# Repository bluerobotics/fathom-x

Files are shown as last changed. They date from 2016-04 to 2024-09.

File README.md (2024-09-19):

# Fathom-X and Fathom-E

The Fathom-X and -E Tether Boards are part of Blue Robotics' *Fathom Tether* system. These boards provide interfaces and functionality for the communication methods used with the tether. With the Fathom tether, it is quick and easy to get up and running and interface with your ROV or other application.

The schematic and board layout are designed in EagleCAD.

# Fathom-E (Simple Ethernet) Hardware

## Description

The Fathom-E board provides a simple and economical way to connect the Fathom Tether or a Cat5 cable to an Ethernet jack. It uses all four twisted pairs in the cable and works for tether lengths of up to 100m (per the Ethernet specification).

# Fathom-X Hardware

The Fathom-X board has a few advantages over the Fathom-E interface. It uses a HomePlugAV (IEEE1901) module to send 100 Mbps Ethernet with a single twisted pair. This robust connection works over at least 300m tether lengths. 

Please see the [official documentation](http://docs.bluerobotics.com/fathom-x/) for more information.

## License

The Fathom Ethernet Hardware Design is released under the MIT License.

## Revision History

### Fathom-E 

rev1 - Works but RJ45 misaligned

rev2 - Production version

### Fathom-X

rev1 - Works but poor tether connector used

rev2 - Production version with updated connector

RevB - In progress

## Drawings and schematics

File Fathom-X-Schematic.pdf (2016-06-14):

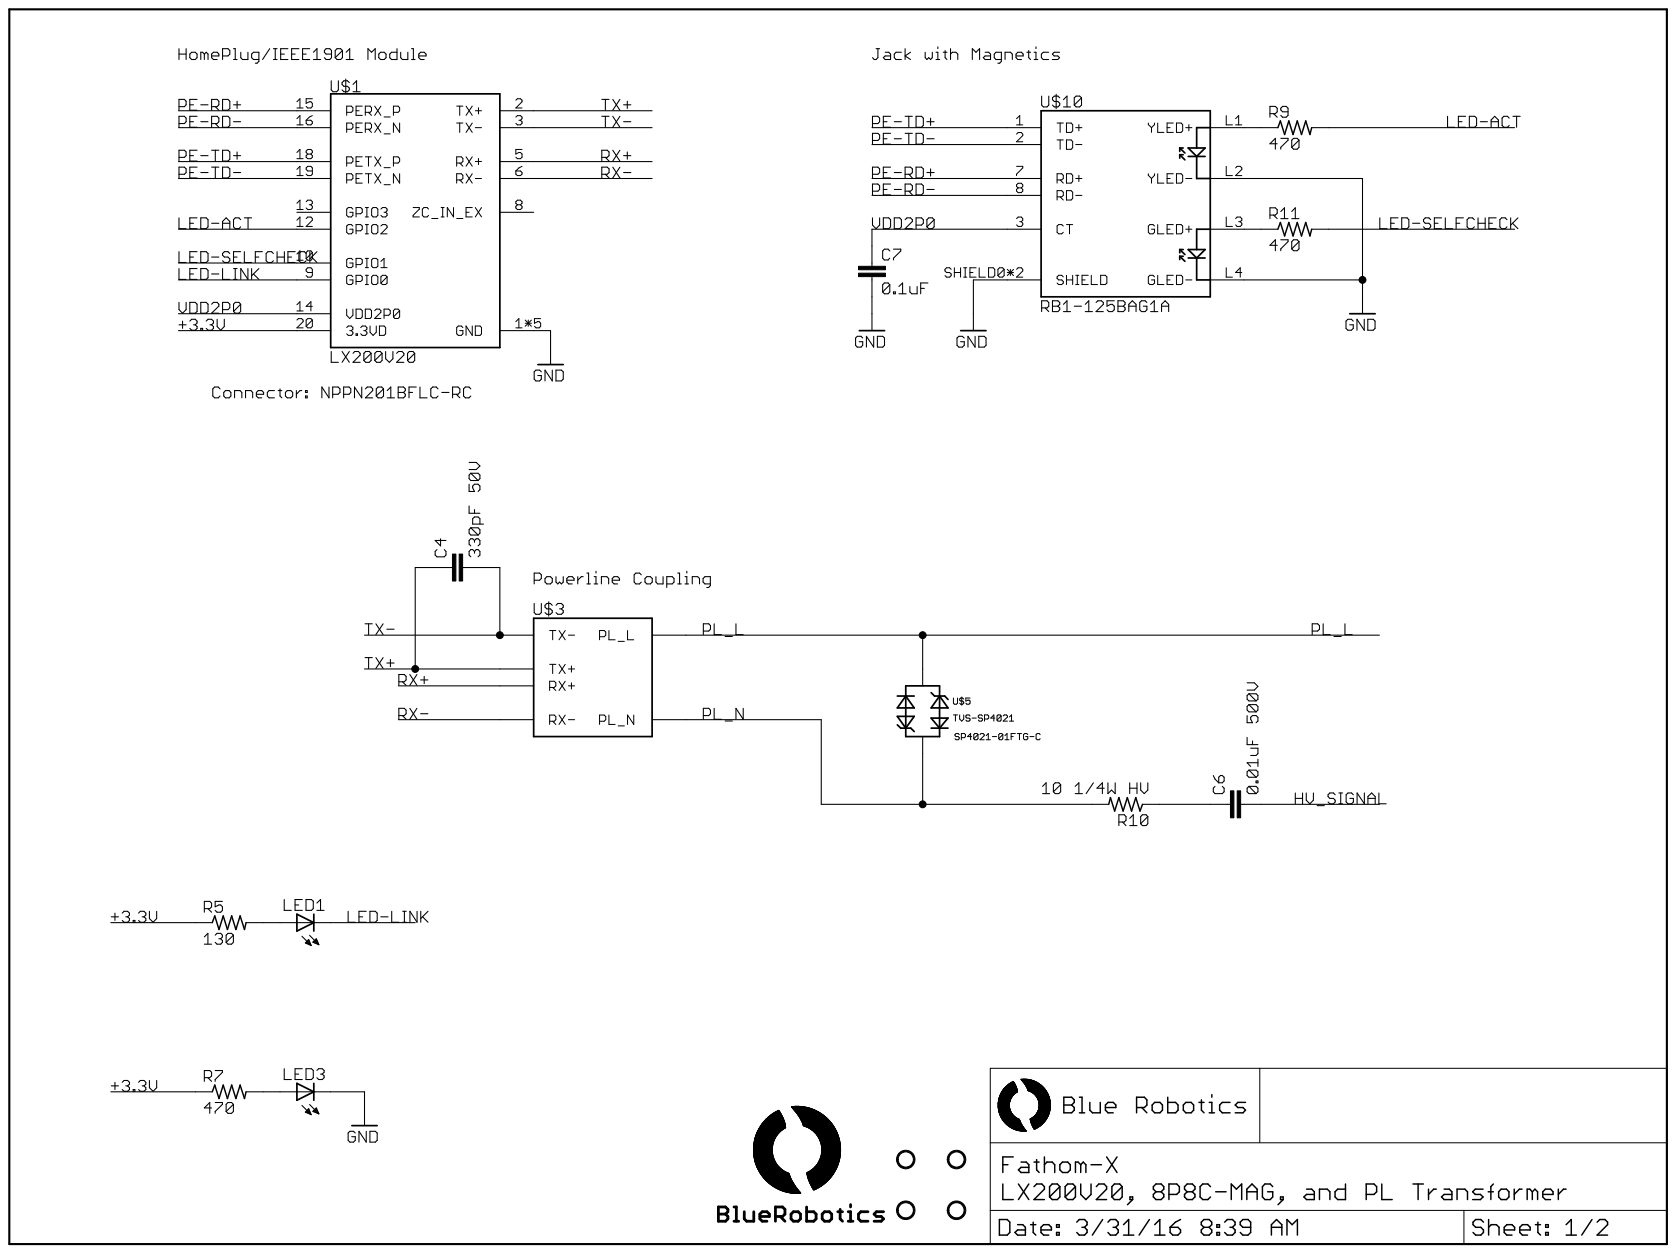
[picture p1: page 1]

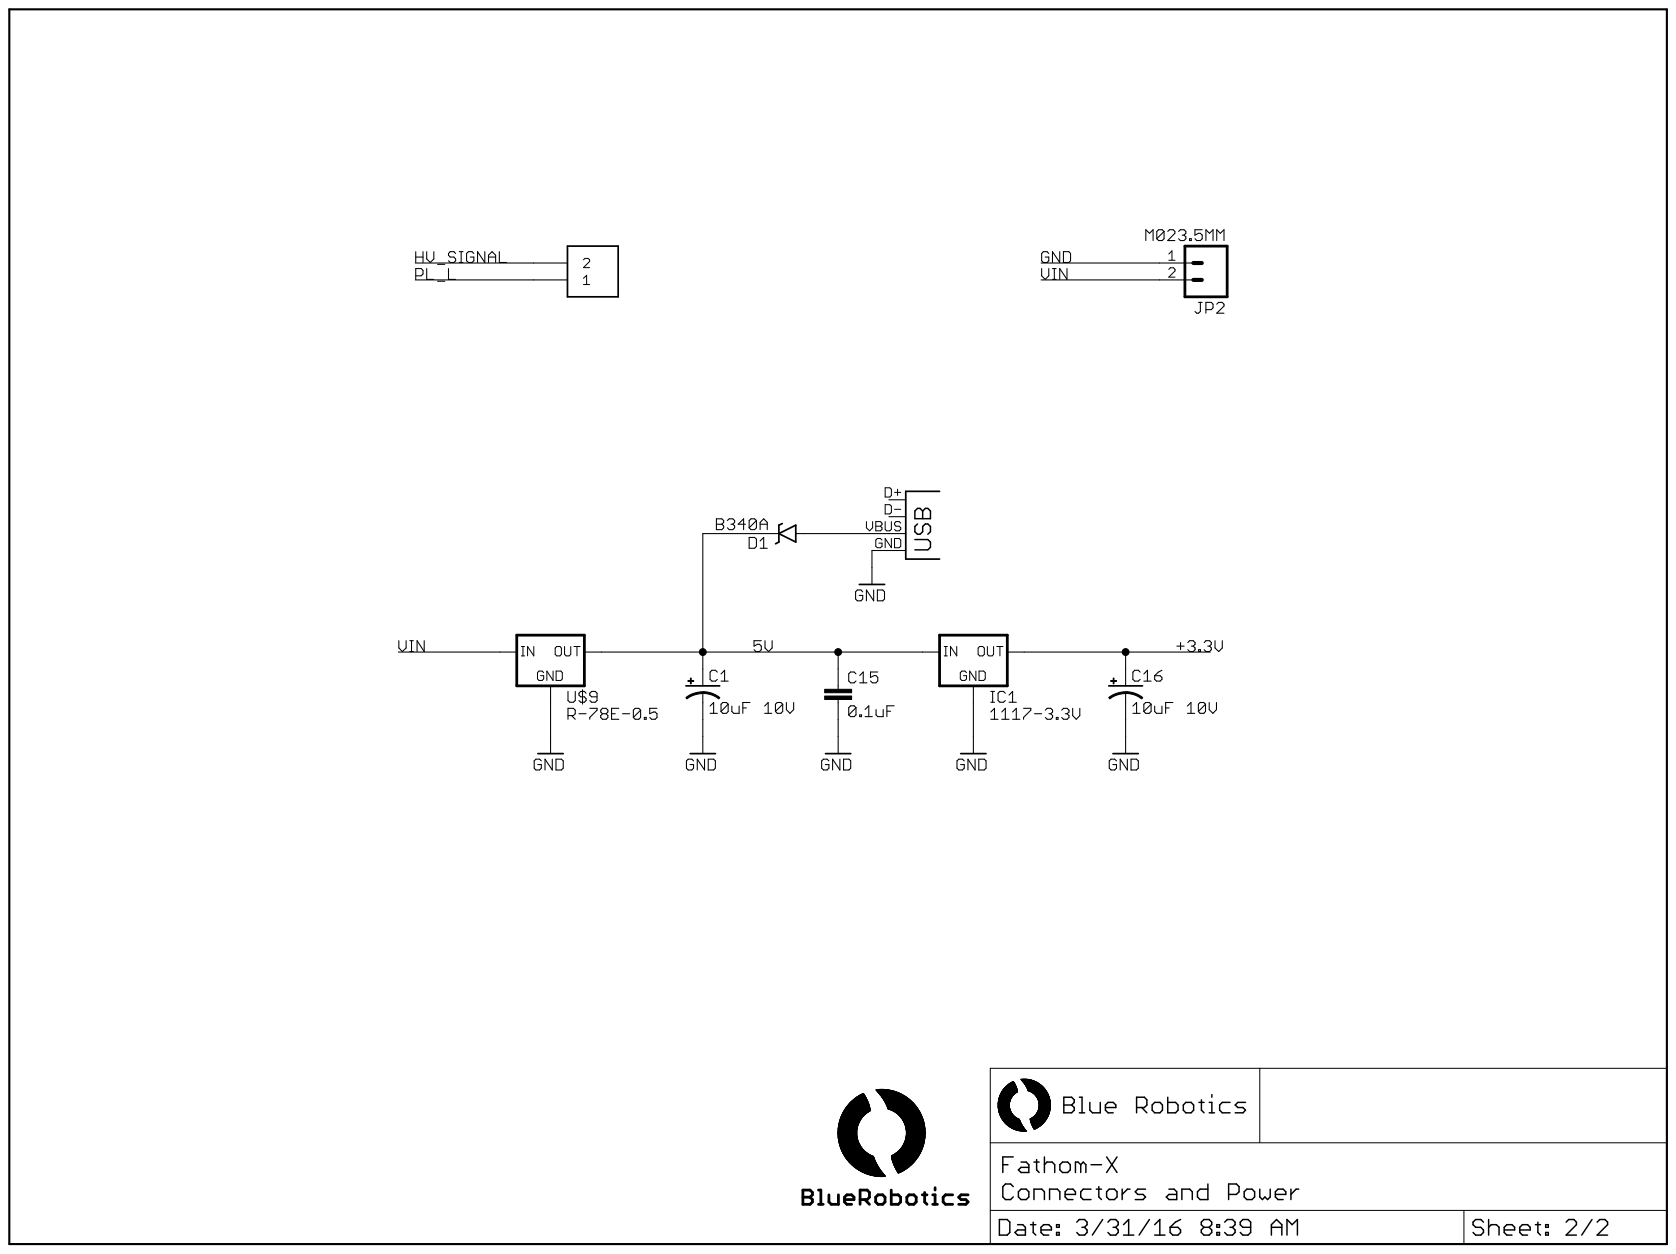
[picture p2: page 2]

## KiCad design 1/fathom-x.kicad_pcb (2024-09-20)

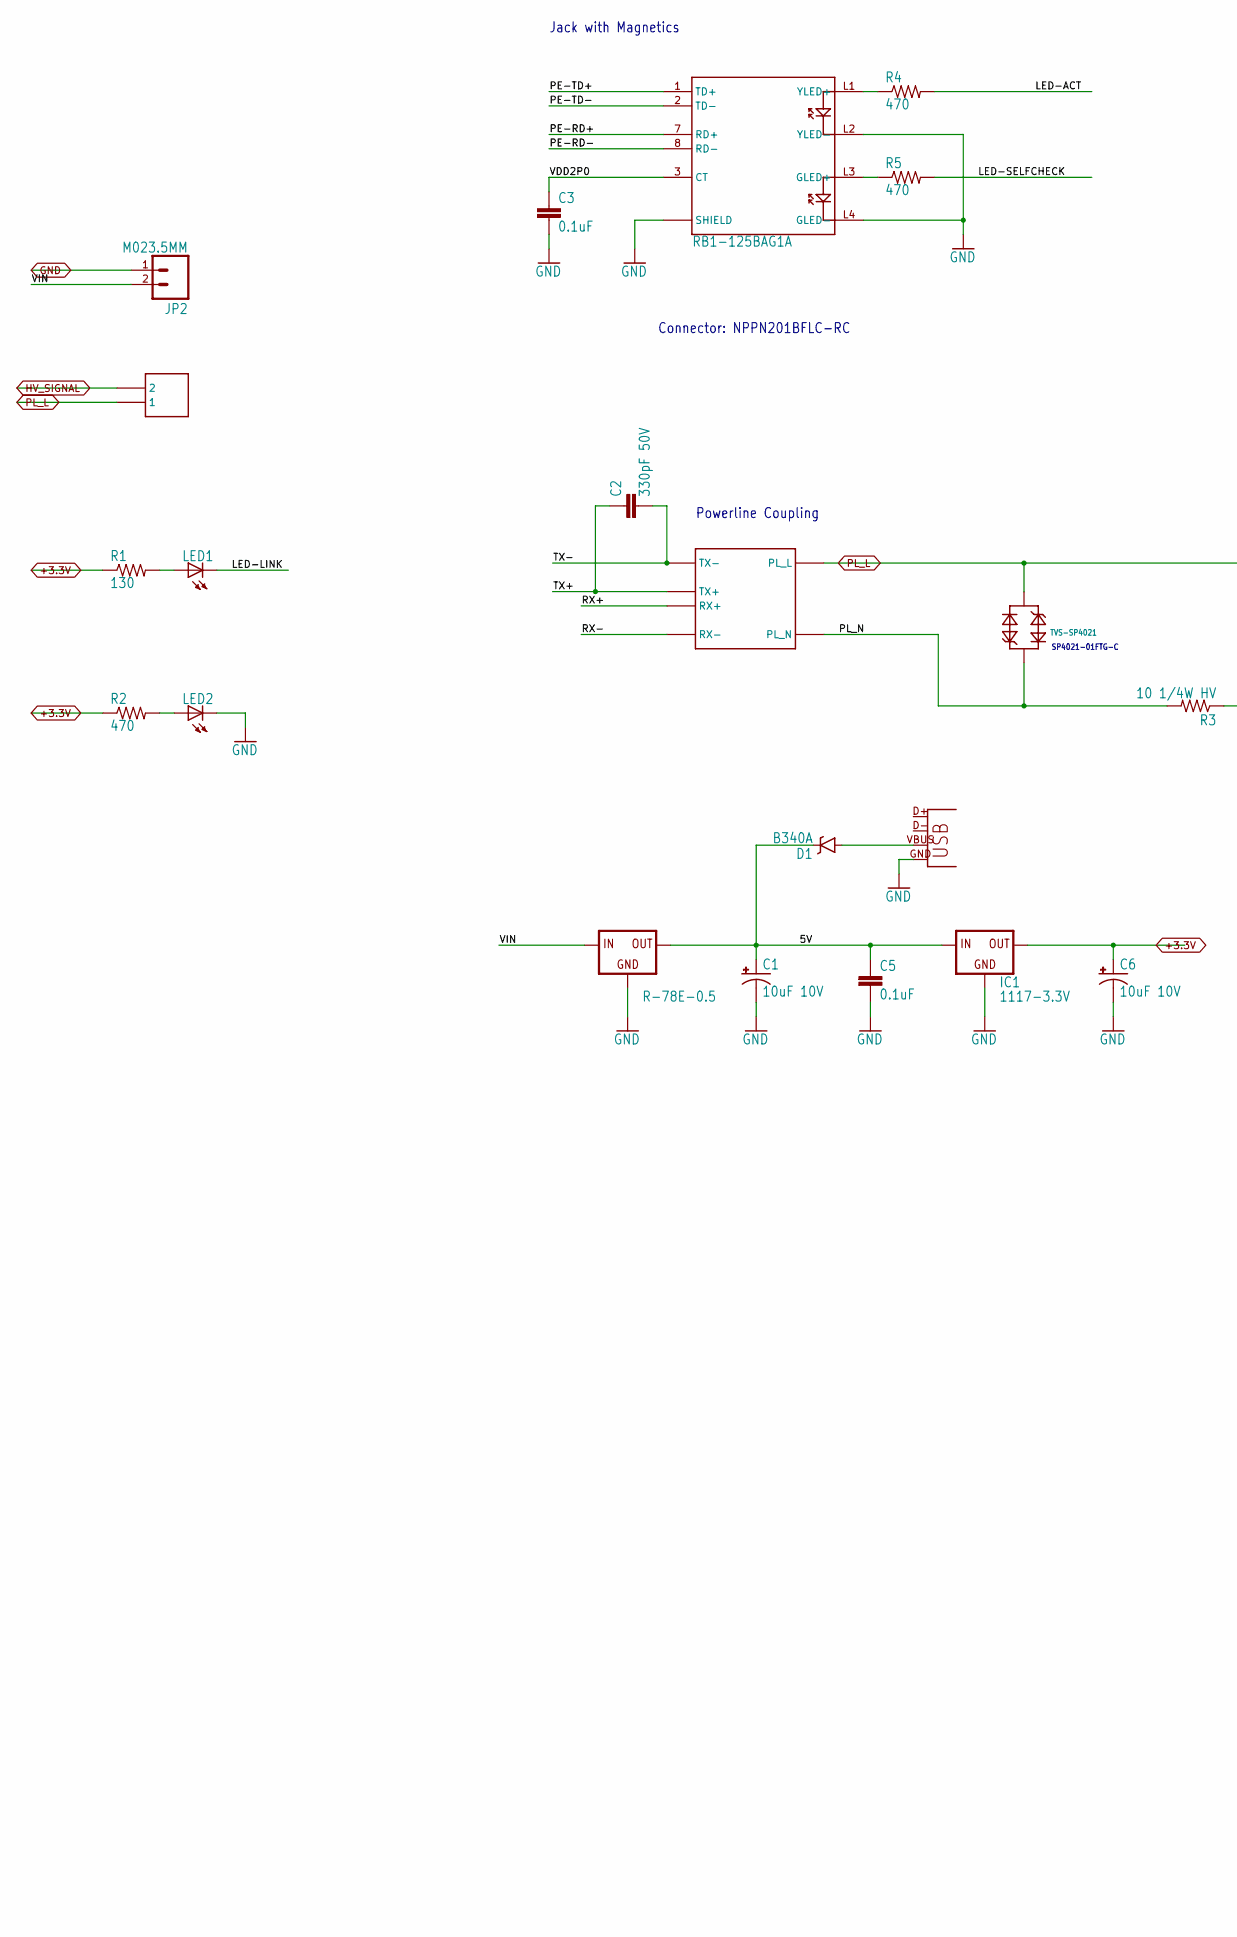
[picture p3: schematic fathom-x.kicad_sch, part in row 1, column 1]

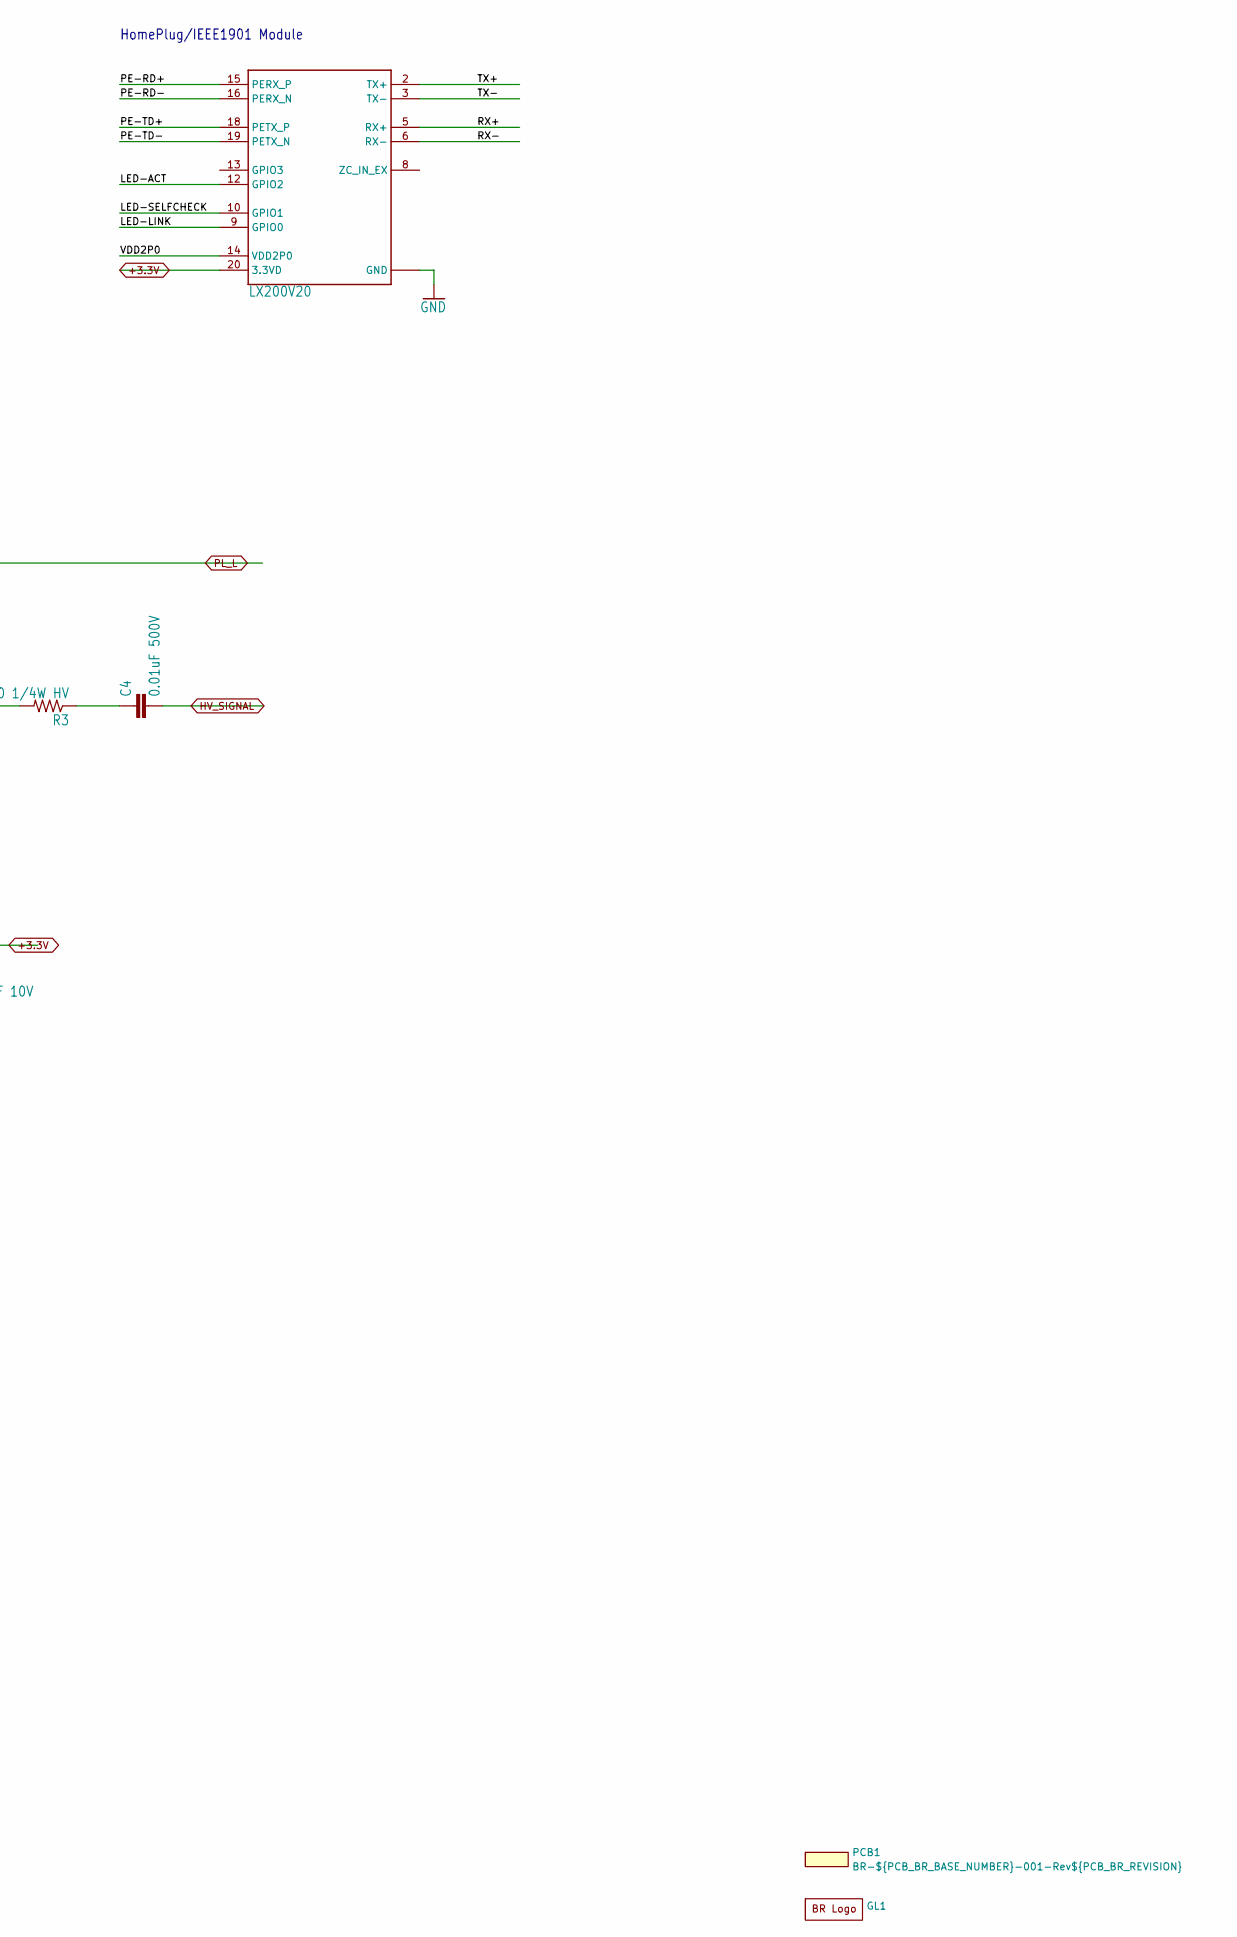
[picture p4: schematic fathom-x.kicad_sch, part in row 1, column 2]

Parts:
C1, C6: 10uF 10V; EIA3216
C2: 330pF 50V; C0805
C3: 0.1uF; C0603
C4: 0.01uF 500V; C1206
C5: 0.1uF; 0603-CAP
D1: B340A; SMA-DIODE
GL1: BR_Logo
IC1: 1117-3.3V; SOT223
JP1: USBSMD; USB-MINIB
JP2: M023.5MM; SCREWTERMINAL-3.5MM-2
LED1, LED2: LEDCHIPLED_0603; CHIPLED_0603
PCB1: Unpopulated PCB; BR_NUMS; Manufacturer Part Num BR-${PCB_BR_BASE_NUMBER}-001-Rev${PCB_B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
R1: 130; R0603
R2, R4, R5: 470; R0603
R3: 10 1/4W HV; R1206
U$1: LX200V20
U$2: UT11403S
U$4: TVS-SP4021; SOD323-BIDIRECTIONAL
U$5: RB1-125BAG1A; RJ45-MAG-WIZNET
U$6: R-78E-0.5
U$8: HEADER-210.16MM; HEADER-10.16MM-2POS

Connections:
+3.3V: C6.A (+), IC1.2 (OUT), R1.1, R2.1, U$1.20 (3.3VD)
/5V: C1.A (+), C5.1, D1.C, IC1.3 (IN), U$6.VOUT (OUT)
/LED-ACT: R4.2, U$1.12 (GPIO2)
/LED-LINK: LED1.C, U$1.9 (GPIO0)
/LED-SELFCHECK: R5.2, U$1.10 (GPIO1)
/PE-RD+: U$1.15 (PERX_P), U$5.7 (RD+)
/PE-RD-: U$1.16 (PERX_N), U$5.8 (RD-)
/PE-TD+: U$1.18 (PETX_P), U$5.1 (TD+)
/PE-TD-: U$1.19 (PETX_N), U$5.2 (TD-)
/PL_N: R3.2, U$2.PL_N, U$4.1
/RX+: U$1.5 (RX+), U$2.RX+
/RX-: U$1.6 (RX-), U$2.RX-
/TX+: C2.1, U$1.2 (TX+), U$2.TX+
/TX-: C2.2, U$1.3 (TX-), U$2.TX-
/VDD2P0: C3.1, U$1.14 (VDD2P0), U$5.3 (CT)
/VIN: JP2.2, U$6.VIN (IN)
GND: C1.C (-), C3.2, C5.2, C6.C (-), IC1.1 (GND), JP1.GND, JP2.1, LED2.C, U$1.1 (GND), U$1.4 (GND), U$1.7 (GND), U$1.11 (GND), U$1.17 (GND), U$5.L2 (YLED-), U$5.L4 (GLED-), U$5.SHIELD0 (SHIELD), U$5.SHIELD1 (SHIELD), U$6.GND
HV_SIGNAL: C4.2, U$8.P$2 (2)
unnamed: C4.1, R3.1
unnamed: D1.A, JP1.VBUS
unnamed: LED1.A, R1.2
unnamed: LED2.A, R2.2
unnamed: R5.1, U$5.L3 (GLED+)
unnamed: R4.1, U$5.L1 (YLED+)
PL_L: U$2.PL_L, U$4.2, U$8.P$1 (1)

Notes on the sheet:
Connector: NPPN201BFLC-RC
Jack with Magnetics
SP4021-01FTG-C
HomePlug/IEEE1901 Module
Powerline Coupling

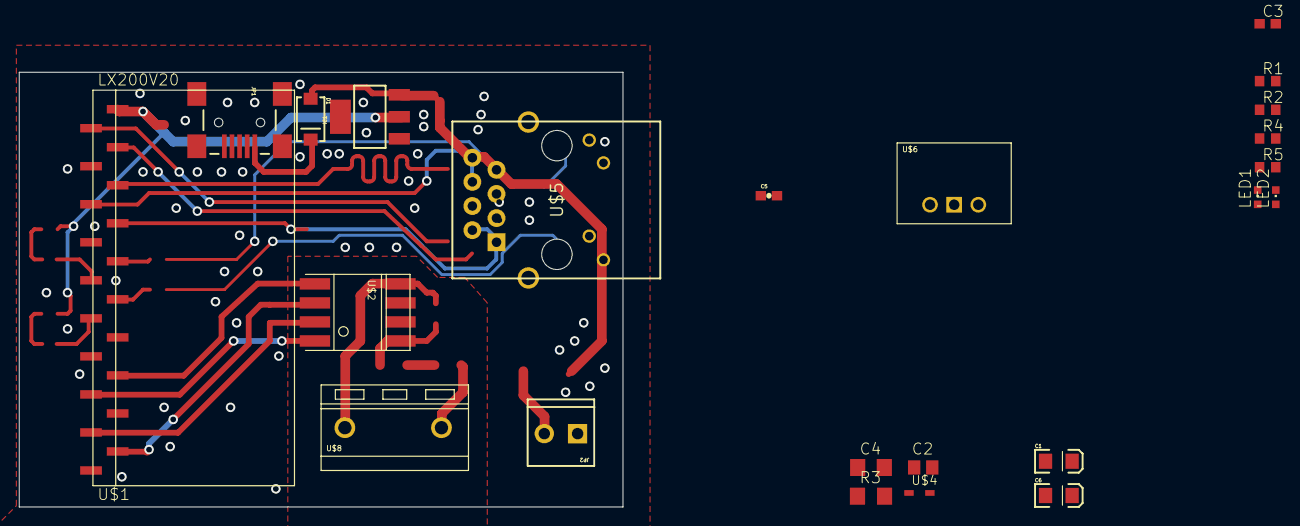
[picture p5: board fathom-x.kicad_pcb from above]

Board: 2 copper layers, 63.5 x 45.7 mm, 25 parts (0 on the bottom side), 25 nets.

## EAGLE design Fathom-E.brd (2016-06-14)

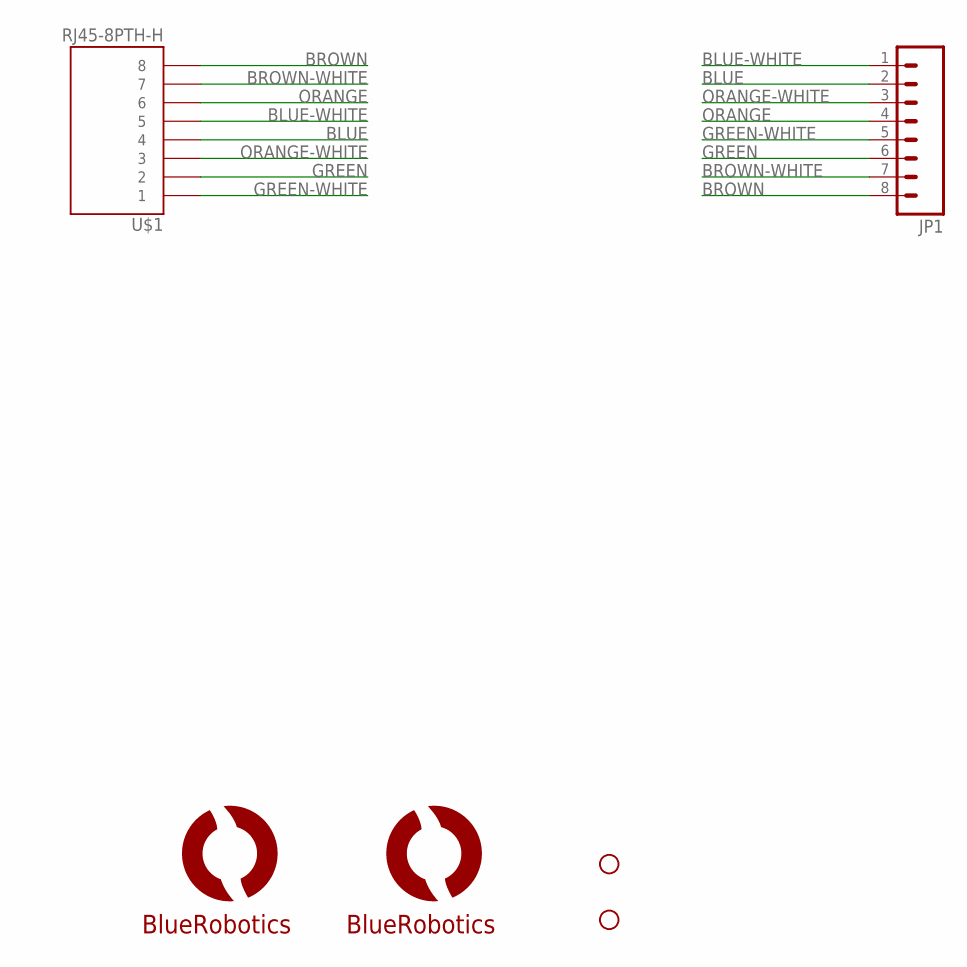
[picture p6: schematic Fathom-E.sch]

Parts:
JP1: M083.5MM-8; SCREWTERMINAL-3.5MM-8
STANDOFF2, STANDOFF3: STAND-OFF
U$1: RJ45-8PTH-H; RJ45-8
U$6: LOGOBR-LOGO-MS-COPPER; BR-LOGO-MEDIUM-SMALL-COPPER
U$7: LOGOFULL-M; BR-FULL-LOGO-MEDIUM

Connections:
BLUE: JP1.2, U$1.4
BLUE-WHITE: JP1.1, U$1.5
BROWN: JP1.8, U$1.8
BROWN-WHITE: JP1.7, U$1.7
GREEN: JP1.6, U$1.2
GREEN-WHITE: JP1.5, U$1.1
ORANGE: JP1.4, U$1.6
ORANGE-WHITE: JP1.3, U$1.3

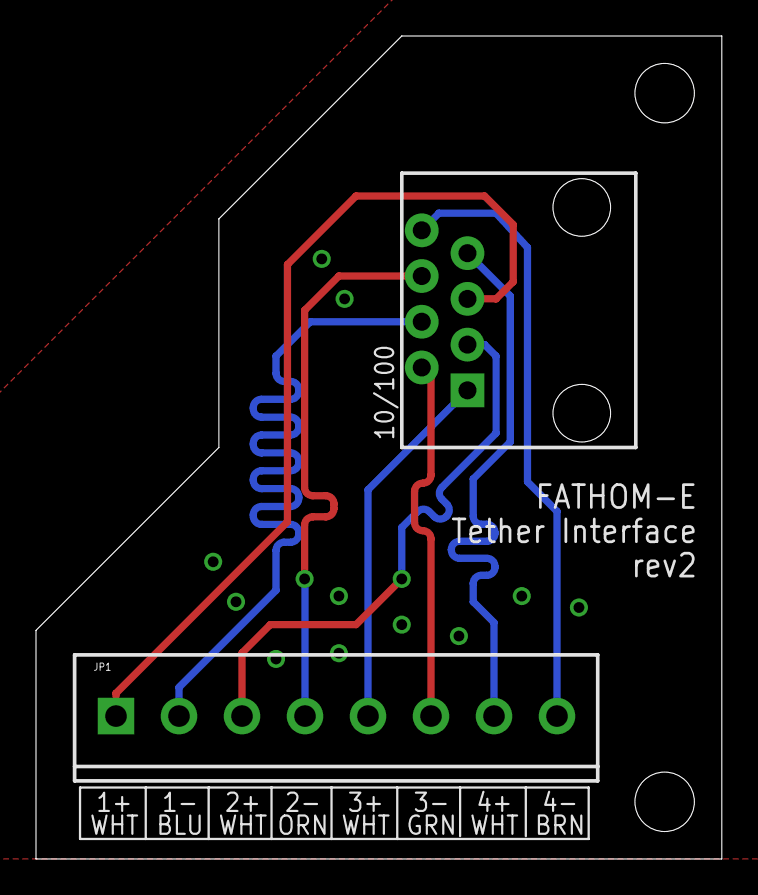
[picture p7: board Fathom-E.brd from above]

Board: 2 copper layers, 38.1 x 45.7 mm, 6 parts (1 on the bottom side), 8 nets.

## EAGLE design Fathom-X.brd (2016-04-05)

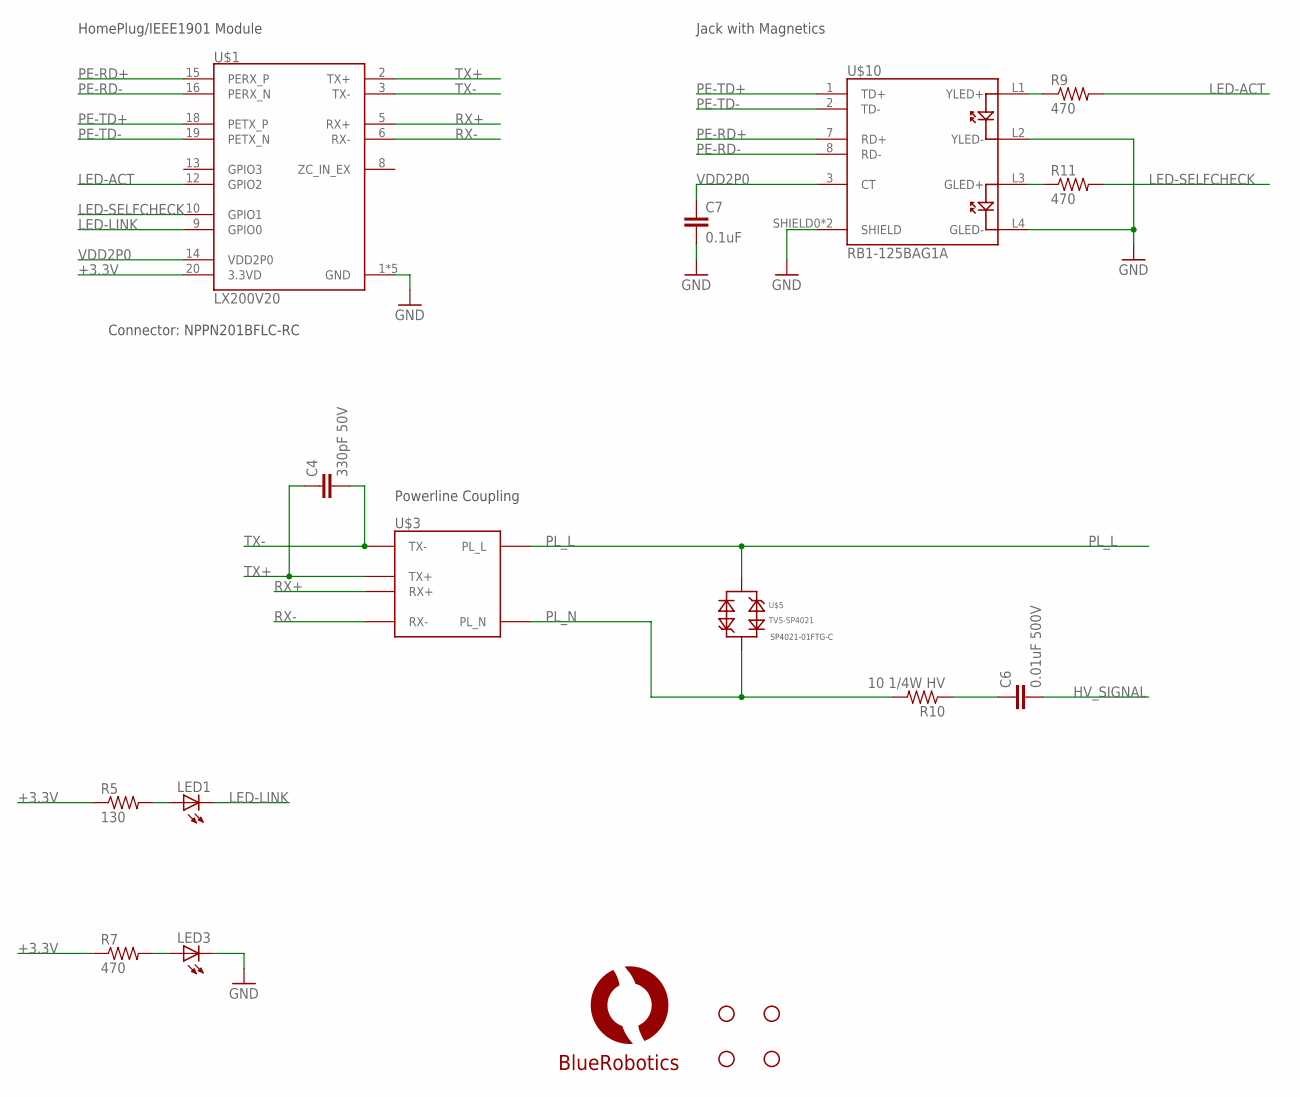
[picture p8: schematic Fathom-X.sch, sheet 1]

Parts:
C4: 330pF 50V; C0805
C6: 0.01uF 500V; C1206
C7: 0.1uF; C0603
LED1, LED3: LEDCHIPLED_0603; CHIPLED_0603
R5: 130; R0603
R7, R9, R11: 470; R0603
R10: 10 1/4W HV; R1206
STANDOFF1, STANDOFF2, STANDOFF3, STANDOFF5: STAND-OFF
U$1: LX200V20
U$3: UT11403S
U$5: TVS-SP4021; SOD323-BIDIRECTIONAL
U$6: LOGOBR-LOGO-MS-COPPER; BR-LOGO-MEDIUM-SMALL-COPPER
U$10: RB1-125BAG1A; RJ45-MAG-WIZNET

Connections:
+3.3V: R5.1, R7.1, U$1.20 (3.3VD); also elsewhere on the board
GND: C7.2, LED3.C, U$1.1 (GND), U$1.4 (GND), U$1.7 (GND), U$1.11 (GND), U$1.17 (GND), U$10.L2 (YLED-), U$10.L4 (GLED-), U$10.SHIELD0 (SHIELD), U$10.SHIELD1 (SHIELD); also elsewhere on the board
HV_SIGNAL: C6.2; also elsewhere on the board
LED-ACT: R9.2, U$1.12 (GPIO2)
LED-LINK: LED1.C, U$1.9 (GPIO0)
LED-SELFCHECK: R11.2, U$1.10 (GPIO1)
unnamed: LED1.A, R5.2
unnamed: LED3.A, R7.2
unnamed: C6.1, R10.1
unnamed: R9.1, U$10.L1 (YLED+)
unnamed: R11.1, U$10.L3 (GLED+)
PE-RD+: U$1.15 (PERX_P), U$10.7 (RD+)
PE-RD-: U$1.16 (PERX_N), U$10.8 (RD-)
PE-TD+: U$1.18 (PETX_P), U$10.1 (TD+)
PE-TD-: U$1.19 (PETX_N), U$10.2 (TD-)
PL_L: U$3.PL_L, U$5.2; also elsewhere on the board
PL_N: R10.2, U$3.PL_N, U$5.1
RX+: U$1.5 (RX+), U$3.RX+
RX-: U$1.6 (RX-), U$3.RX-
TX+: C4.1, U$1.2 (TX+), U$3.TX+
TX-: C4.2, U$1.3 (TX-), U$3.TX-
VDD2P0: C7.1, U$1.14 (VDD2P0), U$10.3 (CT)

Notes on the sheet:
SP4021-01FTG-C
Connector: NPPN201BFLC-RC
HomePlug/IEEE1901 Module
Jack with Magnetics
Powerline Coupling

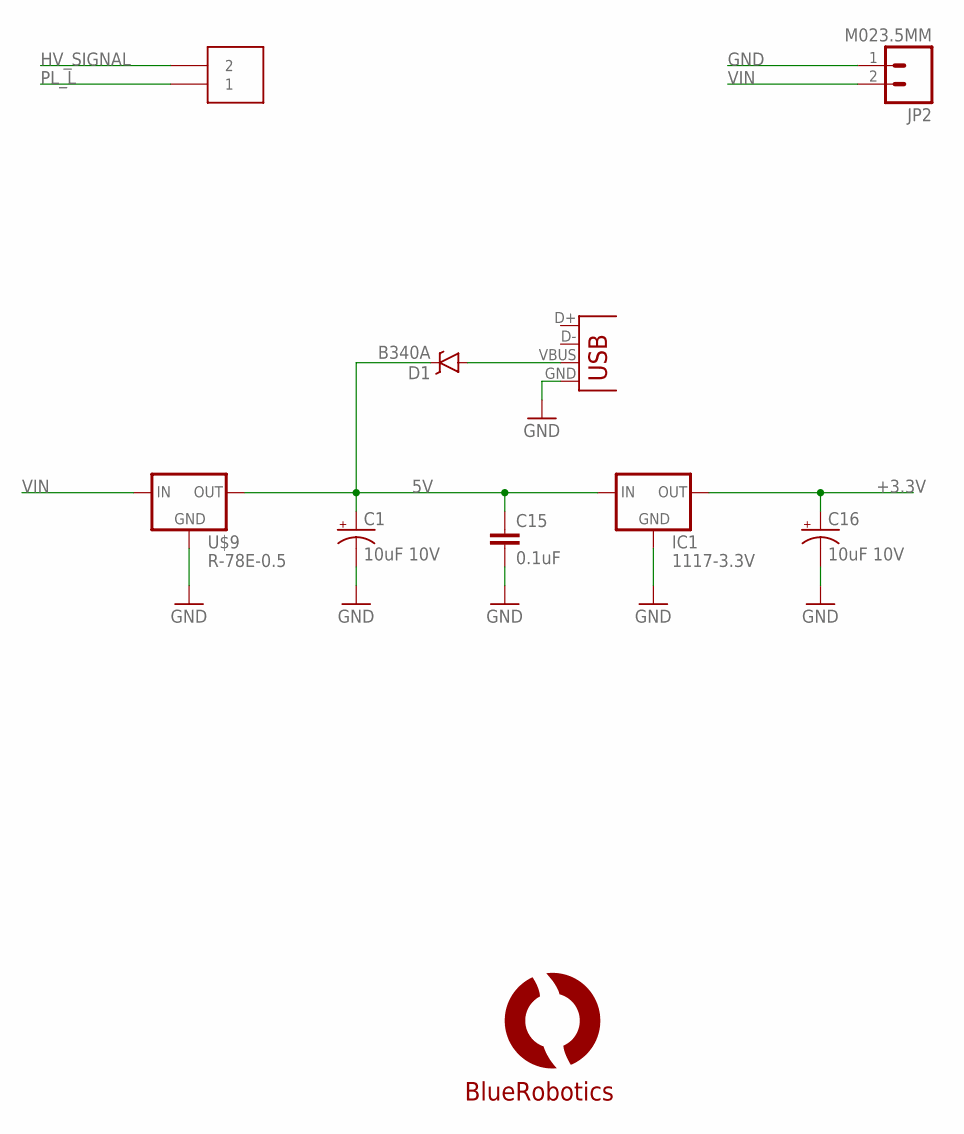
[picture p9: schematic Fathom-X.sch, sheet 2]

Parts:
C1, C16: 10uF 10V; EIA3216
C15: 0.1uF; 0603-CAP
D1: B340A; SMA-DIODE
IC1: 1117-3.3V; SOT223
JP2: M023.5MM; SCREWTERMINAL-3.5MM-2
JP3: USBSMD; USB-MINIB
U$7: LOGOFULL-M; BR-FULL-LOGO-MEDIUM
U$8: HEADER-210.16MM; HEADER-10.16MM-2POS
U$9: R-78E-0.5

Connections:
5V: C1.A (+), C15.1, D1.C, IC1.3 (IN), U$9.VOUT (OUT)
+3.3V: C16.A (+), IC1.2 (OUT); also elsewhere on the board
GND: C1.C (-), C15.2, C16.C (-), IC1.1 (GND), JP2.1, JP3.GND, U$9.GND; also elsewhere on the board
HV_SIGNAL: U$8.P$2 (2); also elsewhere on the board
unnamed: D1.A, JP3.VBUS
PL_L: U$8.P$1 (1); also elsewhere on the board
VIN: JP2.2, U$9.VIN (IN)

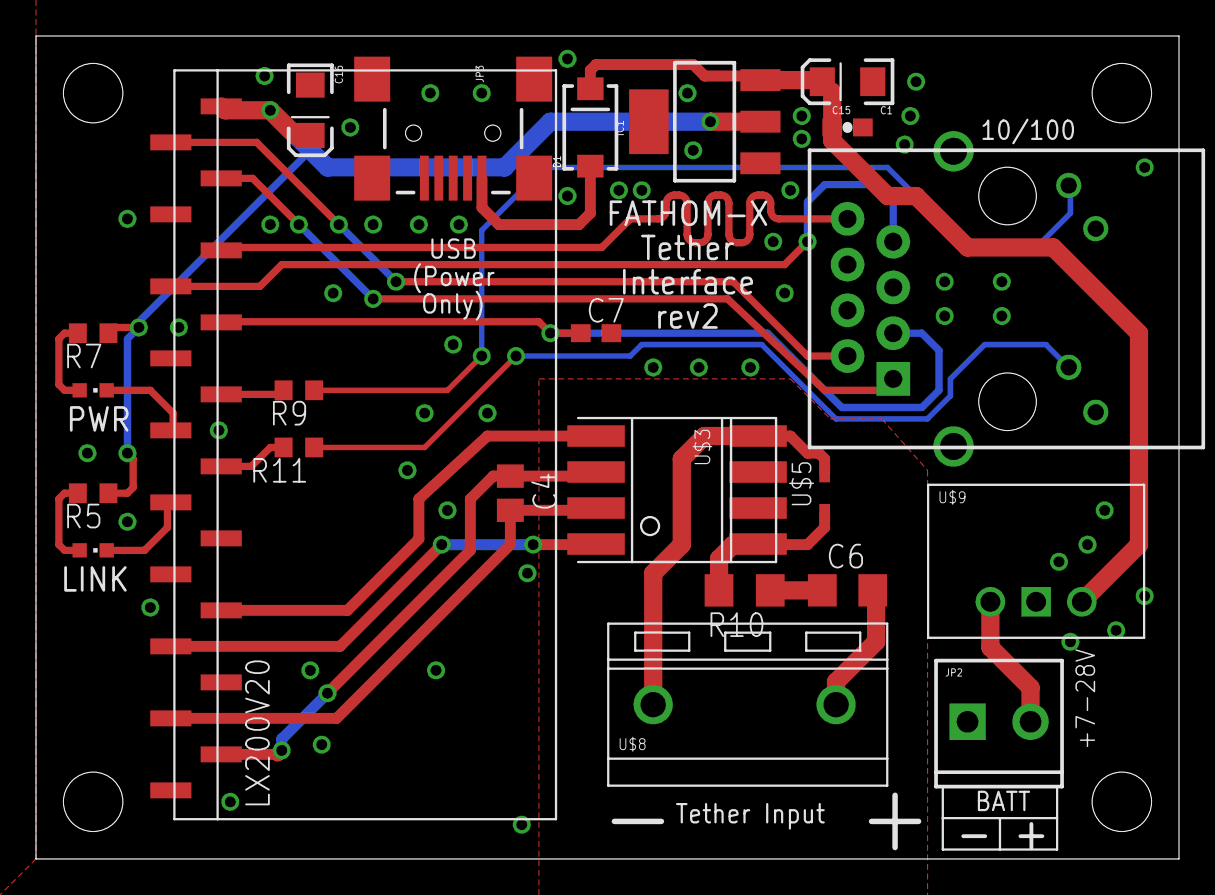
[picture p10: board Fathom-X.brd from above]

Board: 2 copper layers, 63.5 x 45.7 mm, 29 parts (1 on the bottom side), 25 nets.

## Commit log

2016-01-27 Base files for Fathom-E.
    [LX200V20_test.sch]
2016-02-02 First rough layout.
    [LX200V20_test.brd, LX200V20_test.sch]
2016-02-03 Updated layout.
    [LX200V20_test.brd, LX200V20_test.sch]
2016-02-08 Removed AC components for DC-only support.
    [LX200V20_test.brd, LX200V20_test.sch]
2016-02-25 Changing to Ethernet+Power only design.
    [LX200V20_test.brd, LX200V20_test.sch]
2016-03-24 Divide to Fathom-E and Fathom-X. Both boards of this revision were ordered.
    [Fathom-E.brd, Fathom-E.sch, Fathom-X.brd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]
2016-03-24 Fathom-X: Update signal connector
    [Fathom-X.brd, Fathom-X.sch]
2016-03-31 Change connector.
    [Fathom-X.brd, Fathom-X.sch]
2016-04-05 X: Update before order.
    [Fathom-X.brd]
2016-05-05 Updated RJ45 position on Fathom-E
    [Fathom-E.brd, Fathom-E.sch]
2016-06-14 Add Fathom-X schematic.
2016-06-14 Minor Fathom-E change.
    [Fathom-E.brd]
2024-09-19 RevB init
    [Fathom-E.brd, Fathom-E.sch, Fathom-X.brd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]
2024-09-20 did work
    [fathom-x.kicad_pcb, fathom-x.kicad_sch, fathom-x_1.kicad_sch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]
2024-09-25 Updated Fathom-X Eagle parts to Kicad
    [fathom-x.kicad_sch]

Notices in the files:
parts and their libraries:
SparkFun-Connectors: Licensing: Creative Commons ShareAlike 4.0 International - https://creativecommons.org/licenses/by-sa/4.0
